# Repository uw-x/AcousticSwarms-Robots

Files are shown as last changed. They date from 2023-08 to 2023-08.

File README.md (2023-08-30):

## Hardware
The hardware design for the robots used in the acoustic swarms, including the circuits and PCB files.

## Firmware
This subfolder contains the source code for the firmware we upload on the robots. The firmware is compiled and uploaded using [Segger Embedded Studio v7.22](https://www.segger.com/downloads/embedded-studio/) and the [nRF5 SDK v17.0.1](https://www.nordicsemi.com/Products/Development-software/nRF5-SDK/Download#infotabs). 

## Receiver
This subfolder contains the source code and firmware for the receiver used to transmit data to and from the robot swarm. It also contains the 2D robot localization algorithm.

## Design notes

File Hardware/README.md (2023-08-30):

# Robot Hardware
This subfolder contains information pertaining to the robot design files.

## What's included
This folder contains the following directories:

**CAD**: STL files for the 3D models used. The base station is printed using an Ultimaker 3 with white PLA. The rest of the design files use a Formlabs Form 3 printer with black resin. The robot body takes inspiration from [Zooids](https://github.com/ShapeLab/SwarmUI), with various modifications. However, we use the 3D printed wheels are the same.

**Robot**: BoM & PCB design files for the robot main circuit.

**GyroHat**: BoM & PCB design files for the gyroscope hat on the top of the robot.

**SensorBars**: BoM & PCB design files for the sensor bar used to detect edges.

## How to use
To use these circuit design files, you will need the circuit design software KiCad. Simply import the schematics and PCB layouts into your preferred software and you can begin customizing and optimizing the design to fit your specific needs.

<p align="center">
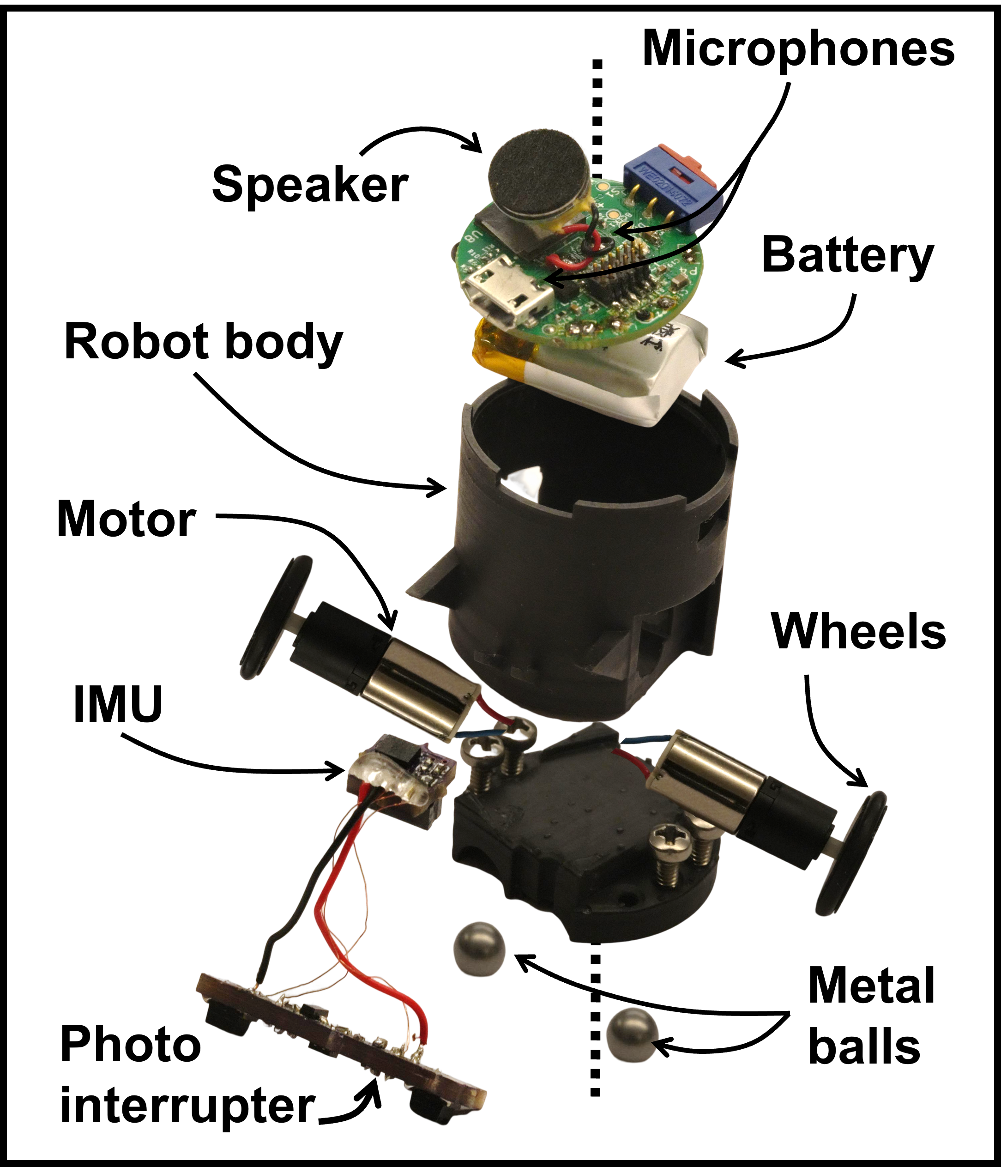
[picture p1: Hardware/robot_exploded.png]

</p>

During assembly, we place two wire connecting the metallic balls at the bottom of the robot to the PCB at the top. One ball is connected to the circuit ground while the other is connected through the +5V battery input (the Vin TestPoint in the PCB). For protection, this ball is connected through a [diode](https://www.digikey.com/ordering/shoppingcart?display=yes&itemSeqs=398627123,398628073,398633233&reprice=2).
We use [micro DC motors](https://www.firgelliauto.com/products/mini-motor-micro-motor) from Firgelli Auto.
We use [M2x0.4mm Thread, 6m Long screws](https://www.mcmaster.com/catalog/129/3394/90116A010) and [1/8 inch diameter aluminium balls](https://www.mcmaster.com/catalog/129/4186/34665K29) from McMaster-Carr.
We use [M1.5x8 Buna-N O-Ring](https://www.amazon.com/gp/product/B00595LLJK/ref=ppx_yo_dt_b_asin_title_o05_s00?ie=UTF8&th=1) from Amazon.

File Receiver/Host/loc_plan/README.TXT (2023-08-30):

1. initialization:
(1) Local_Node:
localization_node = Local_Node(initial_mean, initial_cov, alphas, beta, landmarks, init_angle_available, 'PF')

initial_mean - shape (3, 1), init pos of robot (x, y, theta) - (cm, cm, rad)
initial_cov - shape (3, 3) convariance matrix of init position, can use the example np.diag([0.2**2, 0.2**2, 0.1*2])
alphas - motion noise parameters need to be fine tune in experiment. Initailly use:  alphas = np.array([0.05**2, 0.005**2, 0.3**2, 0.005**2])
beta - chirp ranging noise, Initailly use: beta = np.diag([range_err**2, range_err**2, range_err**2]), where range_err = 0.7 cm
landmarks - shape (3, 2) position of three achors
init_angle_available - True - init angle is known; False - init angle is not known

(2) Planner node:
plan_node = Back_Planner(platform_W, platform_H, init_pos)

platform_W - the width of platform
platform_H - the height of platform
init_pos - the start point of robot, (x, y, theta) 
(destination is defalted by (0, 0))

2. Update 
(1) when the chirp data come, Call:
mean, velocity, particles = localization_node.update_offset(self, sample_offsets, self_offfset, old_pos = None, new_pos = None):

Input:
    sample_offsets - the sample offset from three achors - shape (3, 1)
    self_offfset - the samples offsets from self chirp - single number
    old_pos - the previous est position of robot - shape (3, ) (x, y, theta)
    new_pos - the current est potition of robot - shape (3, ) (x, y, theta)
Output:
    mean - the corretced potition of robot - shape (3, ) - (x, y, theta)
    velocity -  shape (2, 1) est velocity (vx, vy)
    particles - for debugging just ignore

(2) when the correction actions come, Call:
    localization_node.update_milestone(pos)

Input:
    pos - shape (3, ) the est position of the robot before rotating

(3) when the landmarks arrived, Call:

next_milestone, next_next_milestone = plan_node.update_milestone()

Output:
    next_milestone - next milestone, (x,y)
    next_next_milestone - the mile stone after the next milestone. 
The destination is [0, 0], when you is arriving or have arrived at [0, 0], 
the next_milestone returns (0, 0) and next_next_milestone returns (0, 1) for robot go further into the platform

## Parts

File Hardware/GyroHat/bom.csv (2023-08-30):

Component | Description | References | Value | Footprint | Quantity Per PCB | Datasheet | MANUFACTURER
1 | CAP CER 0.1UF 25V X5R 0402 | C2 | 100nF | C_0402_1005Metric | 1 | https://media.digikey.com/pdf/Data%20Sheets/Samsung%20PDFs/CL05A104KA5NNNC.pdf | Samsung Electro-Mechanics
2 | CONN HEADER SMD 12POS 1MM | J1 | FTMH-106-03-L-DV | SAMTEC_FTMH-106-03-L-DV | 1 | https://www.digikey.com/en/products/detail/samtec-inc/FTMH-106-03-L-DV/1104447 | SAMTEC
3 | RES SMD 10K OHM 5% 1/5W 0402 | R1 R2 R3 R4 | 10k | R_0402_1005Metric | 4 | https://fscdn.rohm.com/en/products/databook/datasheet/passive/resistor/chip_resistor/esr-e.pdf | Rohm Semiconductor
4 | INEMO INERTIAL MODULE | U2 | ISM330DLCTR | LGA-14_3x2.5mm_P0.5mm_LayoutBorder3x4y | 1 | https://www.digikey.com/en/products/detail/stmicroelectronics/ISM330DLCTR/7565501 | STMicroelectronics
Component Groups: | 4
Component Count: | 7
Fitted Components: | 7
Number of PCBs: | 1
Total components: | 7
Schematic Version:
Schematic Date:
PCB Variant: | default
BoM Date: | Fri 04 Aug 2023 09:19:59 AM
Schematic Source: | GyroHat.kicad_sch
KiCad Version: | Eeschema 6.0.2+dfsg-1

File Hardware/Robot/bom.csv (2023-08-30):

# | References | Value | Datasheet | Description | Manufacturer | Manufacturer P/N | Vendor | Vendor P/N | Quantity | Notes
1 | > C3, C8 | dnp |  | Do Not Place |  |  |  |  | 2
2 | > C4, C5 | 4.7uF | https://media.digikey.com/pdf/Data%20Sheets/Samsung%20PDFs/CL10A475KQ8NNNC_Spec.pdf | CAP CER 4.7UF 10V X5R 0603 | Samsung Electro-Mechanics | CL10A475KQ8NNNC | Digi-key | 1276-1045-2-ND | 2
3 | C7 | 10uF | https://datasheets.kyocera-avx.com/x6s-dielectric.pdf | CAP CER 10UF 16V X6S 0603 | KYOCERA AVX | 0603YW106MAT2A | Digi-key | 478-0603YW106MAT2ATR-ND | 1
4 | > C1, C2, C6, C10-C12, C14 | 100nF | https://media.digikey.com/pdf/Data%20Sheets/Samsung%20PDFs/CL05A104KA5NNNC.pdf | CAP CER 0.1UF 25V X5R 0402 | Samsung Electro-Mechanics | CL05A104KA5NNNC | Digi-key | 1276-1043-2-ND | 7
5 | J1 | 10118194-0001LF | https://cdn.amphenol-icc.com/media/wysiwyg/files/documentation/datasheet/inputoutput/io_usb_micro.pdf | USB - micro B USB 2.0 Receptacle Connector 5 Position Surface Mount, Right Angle; Through Hole | Amphenol ICC (FCI) | 10118194-0001LF | Digi-key | 609-4618-2-ND | 1
6 | J2 | FTMH-106-03-L-DV | https://www.mouser.com/datasheet/2/527/ftmh_sm-2854321.pdf | Board to Board & Mezzanine Connectors 1.00 mm Surface Mount Micro Terminal Strip | Samtec | FTMH-106-03-L-DV | Mouser | 200-FTMH10603LDV | 1
7 | L1 | 2.2u | https://search.murata.co.jp/Ceramy/image/img/P02/J(E)TE243A-0029_DFE201210U_reference.pdf | 2.2 µH Shielded Wirewound Inductor 1.2 A 228mOhm Max 0805 (2012 Metric) - | Murata Electronics | DFE201210U-2R2M=P2 | Digi-key | 490-16592-2-ND | 1
8 | > MK1, MK2 | ICS-41352 | https://invensense.tdk.com/wp-content/uploads/2016/10/DS-000048-ICS-41352-data-sheet-v1.0.pdf | Bottom Port PDM Low Power muti-Mode Microphone with high AOP Mode | TDK-InvenSense | ICS-41352 | Digi-key | 1428-ICS-41352TR-ND | 2
9 | P1 | BATT_TERM | https://www.jst-mfg.com/product/pdf/eng/eACH.pdf | Connector Header Surface Mount, Right Angle 2 position 0.047" (1.20mm) | JST Sales America Inc. | BM02B-ACHSS-GAN-ETF(LF)(SN | Digi-key | 455-3277-2-ND | 1
10 | P3 | M2_TERM |  | Do Not Place |  |  |  |  | 1 | Solder motor leads here
11 | P4 | M1_TERM |  | Do Not Place |  |  |  |  | 1 | Solder motor leads here
12 | > R1, R3 | 50R | https://www.yageo.com/upload/media/product/productsearch/datasheet/rchip/PYu-AC_51_RoHS_L_10.pdf | RES SMD 50 OHM 5% 1/16W 0402 | YAGEO | AC0402JR-0750RL | Digi-key | 13-AC0402JR-0750RLTR-ND | 2
13 | R2 | 180R | https://www.te.com/usa-en/product-5-2176337-2.datasheet.pdf | RES 180 OHM 1% 1/16W 0402 | TE Connectivity Passive Product | CRGCQ0402F180K | Digi-key | A129654TR-ND | 1
14 | > R4, R5, R7 | 10K | https://fscdn.rohm.com/en/products/databook/datasheet/passive/resistor/chip_resistor/esr-e.pdf | RES SMD 10K OHM 5% 1/5W 0402 | Rohm Semiconductor | ESR01MZPJ103 | Digi-key | RHM1003TR-ND | 3
15 | > R6, R11, R12 | dnp |  | Do Not Place |  |  |  |  | 3
16 | R8 | 100K | https://www.yageo.com/upload/media/product/productsearch/datasheet/rchip/PYu-RT_1-to-0.01_RoHS_L_15.pdf | RES SMD 100K OHM 0.1% 1/16W 0402 | YAGEO | RT0402BRE07100KL | Digi-key | YAG2304TR-ND | 1
17 | > R9, R10, R13 | 0R | https://www.seielect.com/Catalog/SEI-RMCF_RMCP.pdf | RES 0 OHM JUMPER 1/16W 0402 | Stackpole Electronics Inc | RMCF0402ZT0R00 | Digi-key | RMCF0402ZT0R00TR-ND | 3
18 | S1 | 450302014072 | http://www.farnell.com/datasheets/1913864.pdf | Through Hole Slide Switch SPDT On-On 100 mA@ 42 V dc Slide | Wurth Elektronik | 450302014072 | Mouser | 710-450302014072 | 1
19 | SP1 | SPEAKER | http://puiaudio.com/pdf/AS01008MR-3-LW100-R.pdf | 8 Ohms General Purpose Speaker 500 mW 800 Hz ~ 20 kHz Top Round | PUI Audio, Inc. | AS01008MR-3-LW100-R | Digi-key | 668-AS01008MR-3-LW100-R-ND | 1 | Footprint should not match speaker. During fabrication, DO NOT PLACE ANY COMPONENT HERE. Manually solder speaker leads after receiving boards instead.
20 | U1 | B38G3RGB | https://media.digikey.com/pdf/Data%20Sheets/Harvatek%20PDFs/B38G3RGB-10D0003H2U1930%20%20V1.9.pdf | Red, Green, Blue (RGB) - LED Indication - Discrete 2V Red, 3V Green, 3V Blue 0606 (1616 Metric) | Harvatek Corporation | B38G3RGB-10D0003H2U1930 | Digi-key | 3147-B38G3RGB-10D0003H2U1930TR-ND | 1
21 | U2 | LM3671TLX-3.3_NOPB | https://www.ti.com/general/docs/suppproductinfo.tsp?distId=10 | Buck Switching Regulator IC Positive Fixed 3.3V 1 Output 600mA 5-WFBGA, DSBGA | Texas Instruments | LM3671TLX-3.3/NOPB | Digi-key | LM3671TLX-3.3/NOPBTR-ND | 1
22 | U3 | LTC4124 | https://www.analog.com/media/en/technical-documentation/data-sheets/ltc4124.pdf | Wireless Charging ICs 100mA Wireless Li-Ion Charger | Analog Devices | LTC4124EV#TRMPBF | Mouser | 584-LTC4124EV#TRMPBF | 1
23 | U4 | MAX17048G+T10 | https://datasheets.maximintegrated.com/en/ds/MAX17048-MAX17049.pdf | IC BATT MON LI-ION 1CELL 8TDFN | Analog Devices Inc./Maxim Integrated | MAX17048G+T10 | Digi-key | MAX17048G+T10TR-ND | 1
24 | > U5, U6 | DRV8837CDSGR | https://www.ti.com/general/docs/suppproductinfo.tsp?distId=10 | IC HALF-BRIDGE DRVR PWM 8WSON | Texas Instruments | DRV8837CDSGR | Digi-key | 296-47205-2-ND | 2
25 | U7 | MC3419 | https://www.mouser.com/datasheet/2/821/MEMSIC_MC3419_Datasheet-1889799.pdf | Accelerometers Small Digital 3-axis Accelerometer Sensor | MEMSIC | MC3419 | Mouser | 498-MC3419 | 1
26 | U8 | ISP1807-LR-RS | https://www.insightsip.com/fichiers_insightsip/pdf/ble/ISP1807/isp_ble_DS1807.pdf | Bluetooth Bluetooth v5.0, Thread, Zigbee® Transceiver Module 2.402GHz ~ 2.48GHz Integrated, Trace Surface Mount | Insight SIP | ISP1807-LR-RS | Digi-key | 1786-1019-2-ND | 1
27 | U9 | MAX98357A | https://datasheets.maximintegrated.com/en/ds/MAX98357A-MAX98357B.pdf | IC AMP CLASS D MONO 3.2W 9WLP | Analog Devices Inc./Maxim Integrated | MAX98357AEWL+T | Digi-key | MAX98357AEWL+TTR-ND | 1

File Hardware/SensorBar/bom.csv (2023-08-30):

Component | Description | References | Value | Footprint | Quantity Per PCB | Datasheet
1 | CAP CER 0.1UF 25V X5R 0402 | C1 C2 C3 | 100nF | C_0402_1005Metric | 3 | https://media.digikey.com/pdf/Data%20Sheets/Samsung%20PDFs/CL05A104KA5NNNC.pdf
2 | CAP CER 10UF 16V X6S 0603 | C4 | 10uF | C_0402_1005Metric | 1 | https://datasheets.kyocera-avx.com/x6s-dielectric.pdf
3 | TRANS NPN 45V 0.5A TO236AB | Q1 | Q_NPN_BEC | SOT-23 | 1 | https://www.digikey.com/en/products/detail/nexperia-usa-inc/BC817-40-215/763235
4 | RES 100 OHM 1% 1/16W 0402 | R2 R4 | 100 | R_0402_1005Metric | 2 | https://www.vishay.com/docs/28705/mcx0x0xpro.pdf
5 | RES 1K OHM 1% 1/16W 0402 | R1 | 1k | R_0402_1005Metric | 1 | https://www.yageo.com/upload/media/product/productsearch/datasheet/rchip/PYu-AC_51_RoHS_L_10.pdf
6 | RES SMD 10K OHM 5% 1/5W 0402 | R6 R7 R8 | 10k | R_0402_1005Metric | 3 | https://fscdn.rohm.com/en/products/databook/datasheet/passive/resistor/chip_resistor/esr-e.pdf
7 | RES 30K OHM 1% 1/16W 0402 | R3 R5 | 30k | R_0402_1005Metric | 2 | https://www.digikey.com/en/products/detail/yageo/RC0402FR-0730KL/726586
8 | PHOTOINTERRUPTER REFLEC 3MM SMD | U1 U2 | GP2S700HCP | GP2S700HCP | 2 | https://global.sharp/products/device/lineup/data/pdf/datasheet/gp2s700hcp_e.pdf
9 | IC COMPARATOR 2 GEN PUR 8UFSON | U3 | LM293QT | DFN-8-1EP_2x2mm_P0.5mm_EP0.6x1.2mm | 1 | https://www.st.com/content/ccc/resource/technical/document/datasheet/group1/b4/cc/cf/13/18/28/44/f5/CD00000465/files/CD00000465.pdf/jcr:content/translations/e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
Component Groups: | 10
Component Count: | 17
Fitted Components: | 16
Number of PCBs: | 1
Total components: | 16
Schematic Version:
Schematic Date:
PCB Variant: | default
BoM Date: | Fri 04 Aug 2023 09:10:59 AM
Schematic Source: | SensorBar.kicad_sch
KiCad Version: | Eeschema 6.0.2+dfsg-1

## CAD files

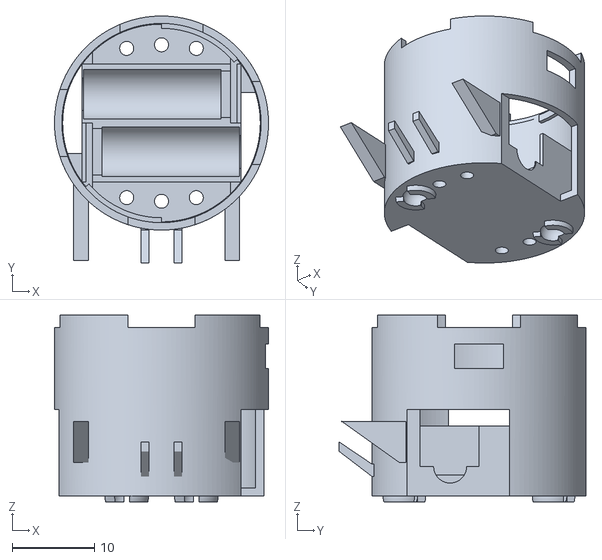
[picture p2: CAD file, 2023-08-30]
Hardware/CAD/BaseDC-Base.stl
26.0 x 30.0 x 22.7

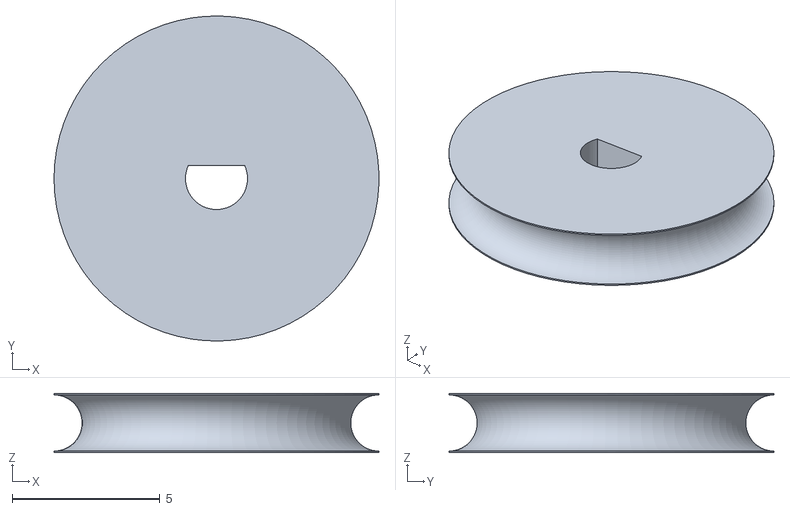
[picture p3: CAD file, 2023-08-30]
Hardware/CAD/WheelWithSlot.STL
11.0 x 11.0 x 2.00

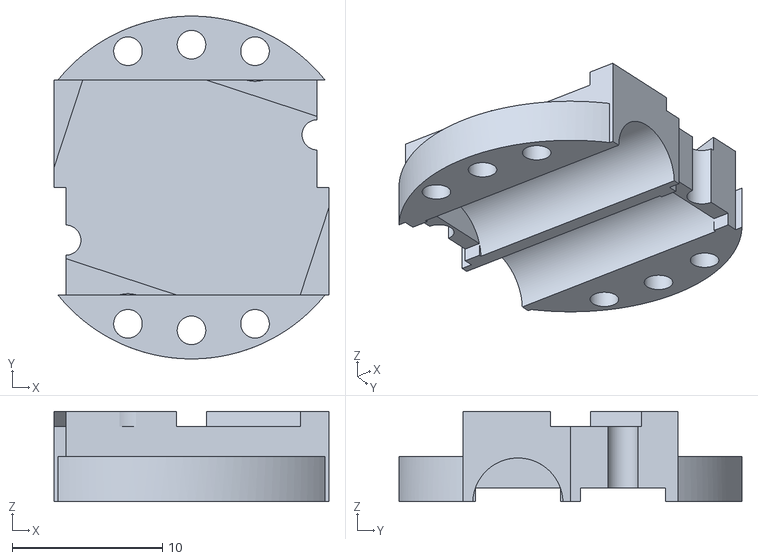
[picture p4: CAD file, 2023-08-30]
Hardware/CAD/RobotMotorTop.stl
18.3 x 22.8 x 6.00

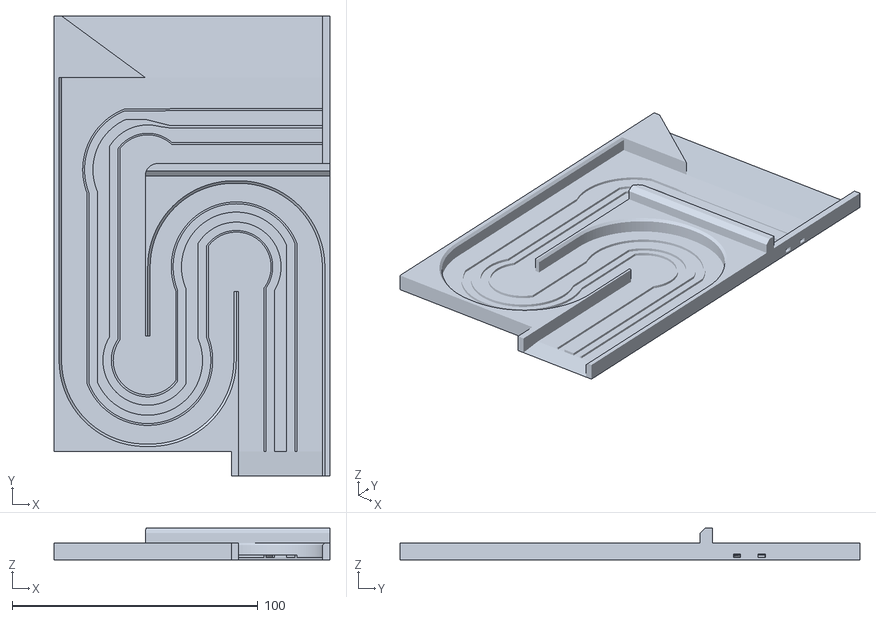
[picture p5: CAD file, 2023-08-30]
Hardware/CAD/Stationv5.3_1.1mm.stl
112.0 x 187.0 x 13.0

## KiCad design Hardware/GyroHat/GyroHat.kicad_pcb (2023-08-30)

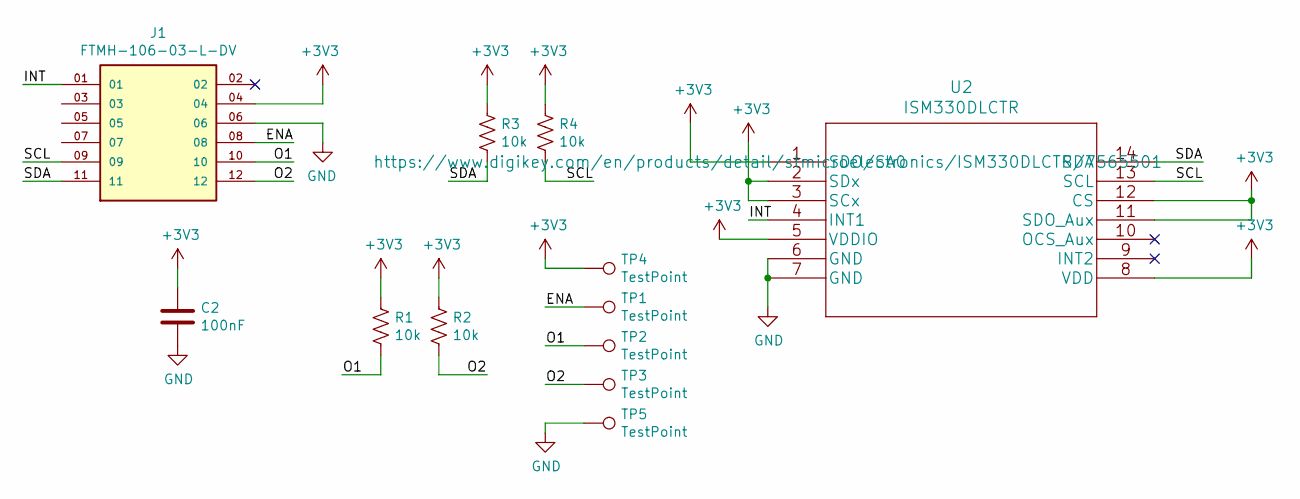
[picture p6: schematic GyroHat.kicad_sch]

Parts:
C2: 100nF; C_0402_1005Metric
J1: FTMH-106-03-L-DV; SAMTEC_FTMH-106-03-L-DV
R1, R2, R3, R4: 10k; R_0402_1005Metric
TP1, TP2, TP3, TP4, TP5: TestPoint; Wire Pad
U2: ISM330DLCTR; LGA-14_3x2.5mm_P0.5mm_LayoutBorder3x4y

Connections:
+3V3: C2.1, J1.04, R1.1, R2.1, R3.1, R4.1, TP4.1, U2.1 (SDO/SA0), U2.2 (SDx), U2.3 (SCx), U2.5 (VDDIO), U2.8 (VDD), U2.11 (SDO_Aux), U2.12 (CS)
/ENA: J1.08, TP1.1
/INT: J1.01, U2.4 (INT1)
/O1: J1.10, R1.2, TP2.1
/O2: J1.12, R2.2, TP3.1
/SCL: J1.09, R4.2, U2.13 (SCL)
/SDA: J1.11, R3.2, U2.14 (SDA)
GND: C2.2, J1.06, TP5.1, U2.6 (GND), U2.7 (GND)

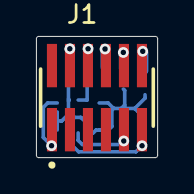
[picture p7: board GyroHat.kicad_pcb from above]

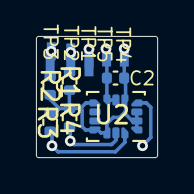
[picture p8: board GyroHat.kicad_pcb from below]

Board: 2 copper layers, 6.7 x 6.7 mm, 12 parts (11 on the bottom side), 8 nets.

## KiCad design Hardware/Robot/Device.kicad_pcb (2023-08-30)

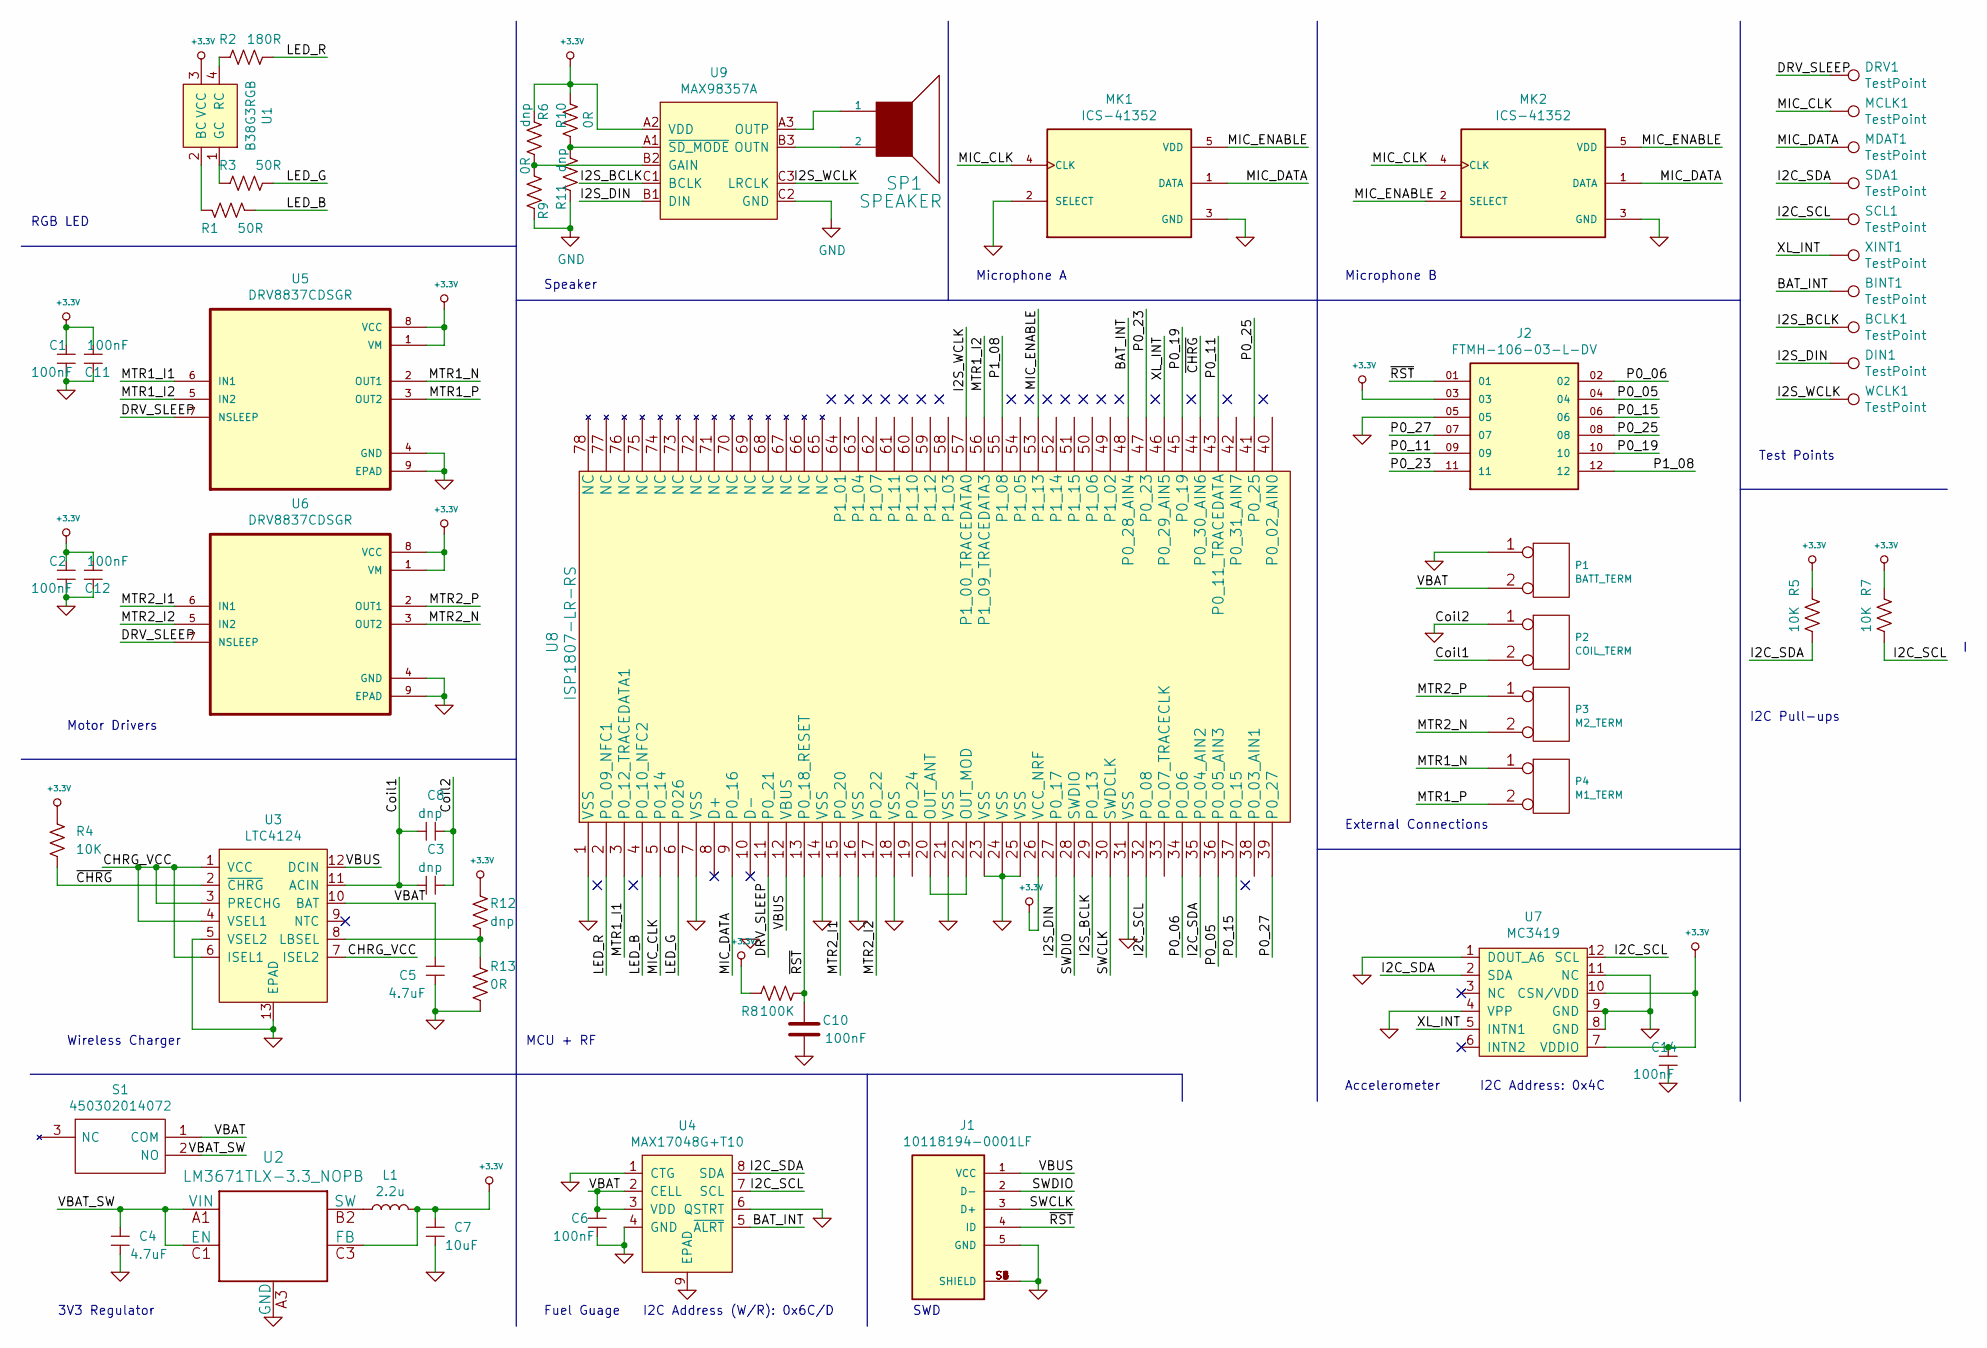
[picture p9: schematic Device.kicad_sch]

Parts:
BCLK1: TestPoint; TestPoint_Pad_D1.0mm
BINT1: TestPoint; TestPoint_Pad_D1.0mm
C1, C2, C6, C10, C11, C12, C14: 100nF; C_0402_1005Metric; Manufacturer P/N CL05A104KA5NNNC
C3, C8: dnp; C_0402_1005Metric
C4, C5: 4.7uF; C_0603_1608Metric; Manufacturer P/N CL10A475KQ8NNNC
C7: 10uF; C_0603_1608Metric; Manufacturer P/N 0603YW106MAT2A
DIN1: TestPoint; TestPoint_Pad_D1.0mm
DRV1: TestPoint; TestPoint_Pad_D1.0mm
J1: 10118194-0001LF; AMPHENOL_10118194-0001LF; PARTREV B
J2: FTMH-106-03-L-DV; SAMTEC_FTMH-106-03-L-DV; Manufacturer P/N FTMH-106-03-L-DV
L1: 2.2u; L_0805_2012Metric; Manufacturer P/N DFE201210U-2R2M=P2
MCLK1: TestPoint; TestPoint_Pad_D1.0mm
MDAT1: TestPoint; TestPoint_Pad_D1.0mm
MK1, MK2: ICS-41352; MIC_ICS-41350; Manufacturer P/N ICS-41352
P1: BATT_TERM; JST_ACH_BM02B-ACHSS-GAN-ETF_1x02-1MP_P1.20mm_Vertical; Manufacturer P/N BM02B-ACHSS-GAN-ETF(LF)(SN
P2: COIL_TERM; TestPoint_2Pads_Pitch2.54mm_Drill0.8mm
P3: M2_TERM; PinHeader_1x02_P1.27mm_Vertical
P4: M1_TERM; PinHeader_1x02_P1.27mm_Vertical
R1, R3: 50R; R_0402_1005Metric; Manufacturer P/N AC0402JR-0750RL
R2: 180R; R_0402_1005Metric; Manufacturer P/N CRGCQ0402F180K
R4, R5, R7: 10K; R_0402_1005Metric; Manufacturer P/N ESR01MZPJ103
R6, R11, R12: dnp; R_0402_1005Metric
R8: 100K; R_0402_1005Metric; Manufacturer P/N RT0402BRE07100KL
R9, R10, R13: 0R; R_0402_1005Metric; Manufacturer P/N RMCF0402ZT0R00
S1: 450302014072; Manufacturer P/N 450302014072
SCL1: TestPoint; TestPoint_Pad_D1.0mm
SDA1: TestPoint; TestPoint_Pad_D1.0mm
SP1: SPEAKER; CUI_CMT-4023S-SMT-TR; Manufacturer P/N SMT-0440-T-HT-R
U1: B38G3RGB; B38G3RGB10D0003H2U1930; Manufacturer P/N B38G3RGB-10D0003H2U1930
U2: LM3671TLX-3.3_NOPB; LM3671TLX-3.3&slash_NOPB; Manufacturer P/N LM3671TLX-3.3/NOPB
U3: LTC4124; LTC4124EV-TRMPBF; Manufacturer P/N LTC4124EV#TRMPBF
U4: MAX17048G+T10; SON50P200X200X80-9N; Manufacturer P/N MAX17048G+T10
U5, U6: DRV8837CDSGR; SON50P200X200X80-9N; Manufacturer P/N DRV8837CDSGR
U7: MC3419; LGA-12_2x2mm_P0.5mm; Manufacturer P/N MC3419
U8: ISP1807-LR-RS; Manufacturer P/N ISP1807-LR-RS
U9: MAX98357A; Maxim_WLP-9_1.595x1.415_Layout3x3_P0.4mm_Ball0.27mm_Pad0.25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; Manufacturer P/N MAX98357AEWL+T
WCLK1: TestPoint; TestPoint_Pad_D1.0mm
XINT1: TestPoint; TestPoint_Pad_D1.0mm

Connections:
+3.3V: C1.1, C2.1, C7.2, C11.2, C12.2, C14.1, J2.03, L1.2, R4.1, R5.1, R6.2, R7.1, R8.1, R10.1, R12.1, U1.3 (VCC), U2.C3 (FB), U5.1 (VM), U5.8 (VCC), U6.1 (VM), U6.8 (VCC), U7.7 (VDDIO), U7.10 (CSN/VDD), U8.26 (VCC_NRF), U9.A2 (VDD)
/BAT_INT: BINT1.1, U4.5 (~ALRT), U8.48 (P0_28_AIN4)
/CHRG_VCC: U3.1 (VCC), U3.3 (PRECHG), U3.4 (VSEL1), U3.6 (ISEL1), U3.7 (ISEL2)
/Coil1: C3.2, C8.2, P2.2 (PM), U3.11 (ACIN)
/DRV_SLEEP: DRV1.1, U5.7 (NSLEEP), U6.7 (NSLEEP), U8.11 (P0_21)
/I2C_SCL: R7.2, SCL1.1, U4.7 (SCL), U7.12 (SCL), U8.32 (P0_08)
/I2C_SDA: R5.2, SDA1.1, U4.8 (SDA), U7.2 (SDA), U8.35 (P0_04_AIN2)
/I2S_BCLK: BCLK1.1, U8.29 (P0_13), U9.C1 (BCLK)
/I2S_DIN: DIN1.1, U8.27 (P0_17), U9.B1 (DIN)
/I2S_WCLK: U8.57 (P1_00_TRACEDATA0), U9.C3 (LRCLK), WCLK1.1
/LED_B: R1.2, U8.4 (P0_10_NFC2)
/LED_G: R3.2, U8.6 (P026)
/LED_R: R2.2, U8.2 (P0_09_NFC1)
/MIC_CLK: MCLK1.1, MK1.4 (CLK), MK2.4 (CLK), U8.5 (P0_14)
/MIC_DATA: MDAT1.1, MK1.1 (DATA), MK2.1 (DATA), U8.9 (P0_16)
/MIC_ENABLE: MK1.5 (VDD), MK2.2 (SELECT), MK2.5 (VDD), U8.53 (P1_13)
/MTR1_I1: U5.6 (IN1), U8.3 (P0_12_TRACEDATA1)
/MTR1_I2: U5.5 (IN2), U8.56 (P1_09_TRACEDATA3)
/MTR1_N: P4.1, U5.2 (OUT1)
/MTR1_P: P4.2 (PM), U5.3 (OUT2)
/MTR2_I1: U6.6 (IN1), U8.15 (P0_20)
/MTR2_I2: U6.5 (IN2), U8.17 (P0_22)
/MTR2_N: P3.2 (PM), U6.3 (OUT2)
/MTR2_P: P3.1, U6.2 (OUT1)
/P0_05: J2.04, U8.36 (P0_05_AIN3)
/P0_06: J2.02, U8.34 (P0_06)
/P0_11: J2.09, U8.43 (P0_11_TRACEDATA)
/P0_15: J2.06, U8.37 (P0_15)
/P0_19: J2.10, U8.45 (P0_19)
/P0_23: J2.11, U8.47 (P0_23)
/P0_25: J2.08, U8.41 (P0_25)
/P0_27: J2.07, U8.39 (P0_27)
/P1_08: J2.12, U8.55 (P1_08)
/SWCLK: J1.3 (D+), U8.30 (SWDCLK)
/SWDIO: J1.2 (D-), U8.28 (SWDIO)
/VBAT: C5.1, C6.2, P1.2 (PM), S1.1 (COM), U3.10 (BAT), U4.2 (CELL), U4.3 (VDD)
/VBAT_SW: C4.2, S1.2 (NO), U2.A1 (VIN), U2.C1 (EN)
/VBUS: J1.1 (VCC), U3.12 (DCIN), U8.12 (VBUS)
/XL_INT: U7.5 (INTN1), U8.46 (P0_29_AIN5), XINT1.1
/~CHRG: R4.2, U3.2 (~CHRG), U8.44 (P0_30_AIN6)
/~RST: C10.1, J1.4 (ID), J2.01, R8.2, U8.13 (P0_18_RESET)
GND: C1.2, C2.2, C3.1, C4.1, C5.2, C6.1, C7.1, C8.1, C10.2, C11.1, C12.1, C14.2, J1.5 (GND), J1.S1 (SHIELD), J1.S2 (SHIELD), J1.S3 (SHIELD), J1.S4 (SHIELD), J1.S5 (SHIELD), J1.S6 (SHIELD), J2.05, MK1.2 (SELECT), MK1.3 (GND), MK2.3 (GND), P1.1, P2.1, R9.1, R11.1, R13.2, U2.A3 (GND), U3.5 (VSEL2), U3.13 (EPAD), U4.1 (CTG), U4.4 (GND), U4.6 (QSTRT), U4.9 (EPAD), U5.4 (GND), U5.9 (EPAD), U6.4 (GND), U6.9 (EPAD), U7.1 (DOUT_A6), U7.4 (VPP), U7.8 (GND), U7.9 (GND), U7.11 (NC), U8.1 (VSS), U8.7 (VSS), U8.14 (VSS), U8.16 (VSS), U8.18 (VSS), U8.21 (VSS), U8.23 (VSS), U8.24 (VSS), U8.25 (VSS), U8.31 (VSS), U9.C2 (GND)
unnamed: L1.1, U2.B2 (SW)
unnamed: R1.1, U1.2 (BC)
unnamed: R2.1, U1.4 (RC)
unnamed: R3.1, U1.1 (GC)
unnamed: R6.1, R9.2, U9.B2 (GAIN)
unnamed: R10.2, R11.2, U9.A1 (~SD_MODE)
unnamed: R12.2, R13.1, U3.8 (LBSEL)
unnamed: SP1.1, U9.A3 (OUTP)
unnamed: SP1.2, U9.B3 (OUTN)
unnamed: U8.20 (OUT_ANT), U8.22 (OUT_MOD)

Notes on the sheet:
3V3 Regulator
I2C Pull-ups
Test Points
Wireless Charger
SWD
MCU + RF
RGB LED
Motor Drivers
Speaker
Fuel Guage
Microphone B
External Connections
Accelerometer
Microphone A
I2C Address: 0x4C
I2C Address (W/R): 0x6C/D

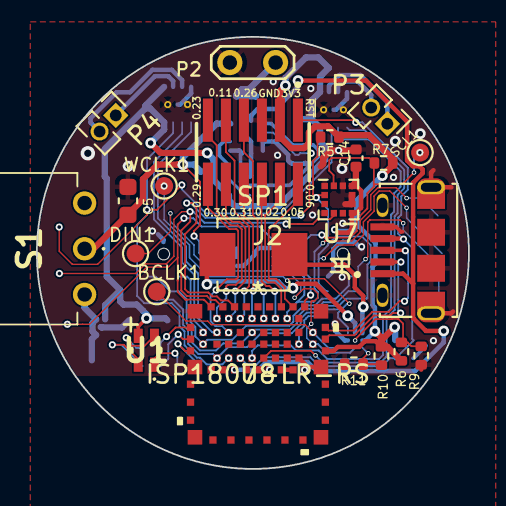
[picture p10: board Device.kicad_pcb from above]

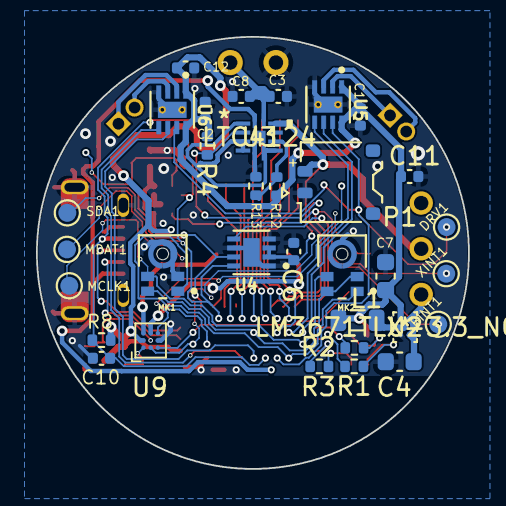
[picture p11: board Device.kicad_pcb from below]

Board: 2 copper layers, 24.0 x 24.0 mm, 55 parts (33 on the bottom side), 52 nets.

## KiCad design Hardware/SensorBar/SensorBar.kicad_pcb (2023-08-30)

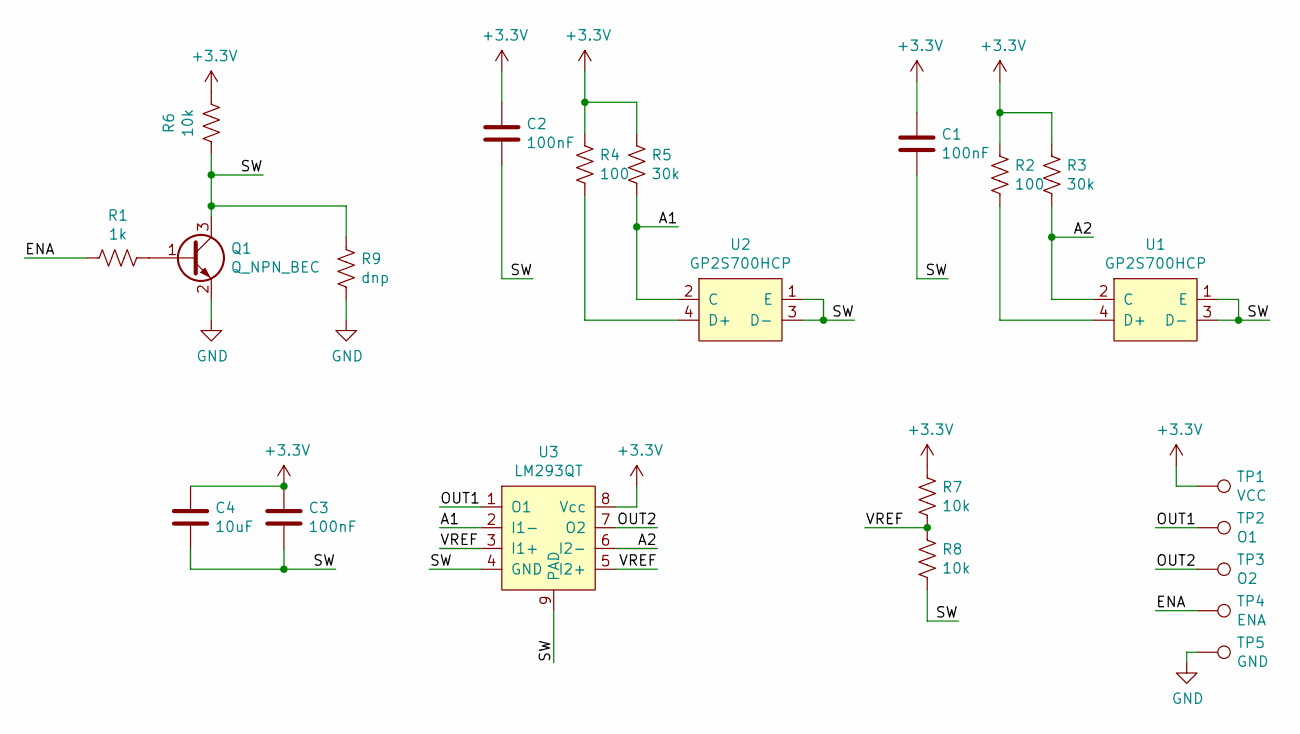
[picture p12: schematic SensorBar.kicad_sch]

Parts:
C1, C2, C3: 100nF; C_0402_1005Metric
C4: 10uF; C_0402_1005Metric
Q1: Q_NPN_BEC; SOT-23
R1: 1k; R_0402_1005Metric
R2, R4: 100; R_0402_1005Metric
R3, R5: 30k; R_0402_1005Metric
R6, R7, R8: 10k; R_0402_1005Metric
R9: dnp; R_0402_1005Metric
TP1: VCC; TestPoint_Pad_D1.0mm
TP2: O1; TestPoint_Pad_D1.0mm
TP3: O2; TestPoint_Pad_D1.0mm
TP4: ENA; TestPoint_Pad_D1.0mm
TP5: GND; TestPoint_Pad_D1.0mm
U1, U2: GP2S700HCP
U3: LM293QT; DFN-8-1EP_2x2mm_P0.5mm_EP0.6x1.2mm

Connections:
+3V3: C1.1, C2.1, C3.1, C4.1, R2.2, R3.2, R4.2, R5.2, R6.1, R7.2, TP1.1, U3.8 (Vcc)
/A1: R5.1, U2.2 (C), U3.2 (I1-)
/A2: R3.1, U1.2 (C), U3.6 (I2-)
/ENA: R1.2, TP4.1
/OUT1: TP2.1, U3.1 (O1)
/OUT2: TP3.1, U3.7 (O2)
/SW: C1.2, C2.2, C3.2, C4.2, Q1.3 (C), R6.2, R8.1, R9.2, U1.1 (E), U1.3 (D-), U2.1 (E), U2.3 (D-), U3.4 (GND), U3.9 (PAD)
/VREF: R7.1, R8.2, U3.3 (I1+), U3.5 (I2+)
GND: Q1.2 (E), R9.1, TP5.1
unnamed: Q1.1 (B), R1.1
unnamed: R2.1, U1.4 (D+)
unnamed: R4.1, U2.4 (D+)

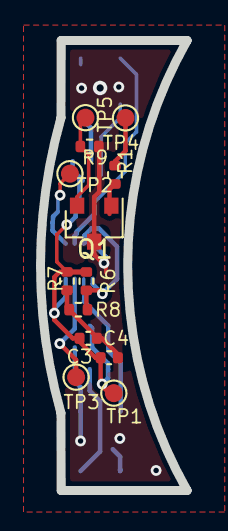
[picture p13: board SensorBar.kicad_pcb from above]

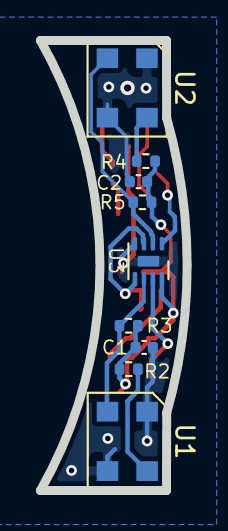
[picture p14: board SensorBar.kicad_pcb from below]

Board: 2 copper layers, 8.1 x 25.0 mm, 22 parts (9 on the bottom side), 12 nets.

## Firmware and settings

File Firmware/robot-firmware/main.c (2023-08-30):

// MAKE SURE ROBOT NAME IS SHIO NOT SHIOG

/**
 * Copyright (c) 2014 - 2021, Nordic Semiconductor ASA
 *
 * All rights reserved.
 *
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
 * 3. Neither the name of Nordic Semiconductor ASA nor the names of its
 *    contributors may be used to endorse or promote products derived from this
 *    software without specific prior written permission.
 *
 * 4. This software, with or without modification, must only be used with a
 *    Nordic Semiconductor ASA integrated circuit.
 *
 * 5. Any software provided in binary form under this license must not be reverse
 *    engineered, decompiled, modified and/or disassembled.
 *
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
 */
/** @file
 *
 * @defgroup ble_sdk_app_template_main main.c
 * @{
 * @ingroup ble_sdk_app_template
 * @brief Template project main file.
 *
 * This file contains a template for creating a new application. It has the code necessary to wakeup
 * from button, advertise, get a connection restart advertising on disconnect and if no new
 * connection created go back to system-off mode.
 * It can easily be used as a starting point for creating a new application, the comments identified
 * with 'YOUR_JOB' indicates where and how you can customize.
 */

 
#include <assert.h>

#include <stdbool.h>
#include <stdint.h>
#include <string.h>

#include "nordic_common.h"
#include "nrf.h"

#include "app_error.h"
#include "nrf_sdh.h"
#include "nrf_sdh_soc.h"
#include "app_timer.h"
#include "app_util_platform.h"

#include "peer_manager.h"
#include "peer_manager_handler.h"
#include "nrf_pwr_mgmt.h"

#include "nrf_log.h"
#include "nrf_log_ctrl.h"
#include "nrf_log_default_backends.h"

#include "nrf_ppi.h"
#include "nrf_timer.h"
#include "nrf_egu.h"

#include "gpio.h"
#include "ble_manager.h"
#include "event.h"
#include "timers.h"
#include "ble_config.h"
#include "time_sync.h"
#include "audio.h"

#include "led.h"
#include "bsp_btn_ble.h"
#include "i2c.h"
#include "i2s.h"
#include "buzzer.h"
#include "fuel_gauge.h"
#include "accel.h"
#include "motors.h"
#include "recorder.h"
#include "ts_tasks.h"
#include "charger.h"
#include "nav.h"
#include "point.h"
#include "gyro.h"
#include "channel_utils.h"
#include "ir.h"
#include "ble_dcs.h"
#include "profile.h"


// In case something is going wrong, check on both receiver & robots:
// Always use stack allocation for ringbuffers!!
// Always compile as release!!

APP_TIMER_DEF(resetTimer);

static uint8_t micData[PACKET_LENGTH];
static bool bleRetry = false;

static bool m_pdm_started = false;
static bool m_stream_started = false;
static uint32_t m_interval = 0;

static bool m_audio_data_requested = false;

// Enough for 250 ms @ 50kHz (as int16)
//#define RECORDING_BUFFER_SIZE 35000

// Enough for 50 ms @ 62.5kHz (as int16)
#define RECORDING_BUFFER_SIZE (6500 * 2)
//#define RECORDING_BUFFER_SIZE 8
static int16_t rec_single_channel_buffer[3126];

#define SHIELD_ENABLED 1

static uint8_t m_record_buffer[RECORDING_BUFFER_SIZE] = {0};
static recording_t s_recording;

static uint64_t expectedBufferCount = 0;

static int64_t m_audio_buffer_samples = 0;

static bool m_sensor_notifications_enabled = false;

/**@brief Callback function for asserts in the SoftDevice.
 *
 * @details This function will be called in case of an assert in the SoftDevice.
 *
 * @warning This handler is an example only and does not fit a final product. You need to analyze
 *          how your product is supposed to react in case of Assert.
 * @warning On assert from the SoftDevice, the system can only recover on reset.
 *
 * @param[in] line_num   Line number of the failing ASSERT call.
 * @param[in] file_name  File name of the failing ASSERT call.
 */
void assert_nrf_callback(uint16_t line_num, const uint8_t * p_file_name)
{
    NRF_LOG_RAW_INFO("DEADBEEF: SOFTDEVICE INTERNAL ERRROR IN %s AT LINE %d\n", p_file_name, line_num);
    app_error_handler(DEAD_BEEF, line_num, p_file_name);
}


/**@brief Function for putting the chip into sleep mode.
 *
 * @note This function will not return.
 */
static void sleep_mode_enter(void)
{
    ret_code_t err_code;

    err_code = led_indicate(LED_OFF);

    // Prepare wakeup buttons.
    //err_code = bsp_btn_ble_sleep_mode_prepare();
    //APP_ERROR_CHECK(err_code);

    // Go to system-off mode (this function will not return; wakeup will cause a reset).
    err_code = sd_power_system_off();
    APP_ERROR_CHECK(err_code);
}


/**@brief Function for initializing the nrf log module.
 */
static void log_init(void)
{
    ret_code_t err_code = NRF_LOG_INIT(NULL);
    APP_ERROR_CHECK(err_code);

    NRF_LOG_DEFAULT_BACKENDS_INIT();
}


/**@brief Function for initializing power management.
 */
static void power_management_init(void)
{
    ret_code_t err_code;
    err_code = nrf_pwr_mgmt_init();
    APP_ERROR_CHECK(err_code);
}

void powerEnterSleepMode(void)
{
  ret_code_t err_code;

  NRF_LOG_RAW_INFO("%08d [power] powering off...\n", systemTimeGetMs());

  err_code = led_indicate(LED_OFF);
  APP_ERROR_CHECK(err_code);
  
  motors_deinit();
  accel_deinit();
  
#if SHIELD_ENABLED
  gyro_deinit();
#endif
  
  // Don't ?
  //fg_deinit();
  
  i2c_deinit();
  i2s_deinit();
  audioDeInit();

  led_deinit();
  ir_disable();

  ////spiDeInit();
  //delayMs(1);

  NRF_LOG_RAW_INFO("%08d [power] Shut down.\n", systemTimeGetMs());
  // Go to system-off mode (this function will not return; wakeup will cause a reset).
  err_code = sd_power_system_off();
  APP_ERROR_CHECK(err_code);
}

/**@brief Function for handling the idle state (main loop).
 *
 * @details If there is no pending log operation, then sleep until next the next event occurs.
 */
static void idle_state_handle(void){
    if (NRF_LOG_PROCESS() == false){
        nrf_pwr_mgmt_run();
    }
}

static void resetTimerCallback(void * p_context){
  NVIC_SystemReset();
}

void TIMER3_IRQHandler(){
  if(NRF_TIMER3->EVENTS_COMPARE[4]){
    if(!ts_sync_tasks_started()){
      ts_sync_tasks_start(true);
      NRF_LOG_RAW_INFO("%08d [main] TIME SYNC MASTER\n", systemTimeGetMs());
    }else{
      NRF_LOG_INFO("Disabling PPIs");
      ts_sync_tasks_disable_pending_ppis();
    }
    NRF_TIMER3->EVENTS_COMPARE[4] = 0;
    // Disable interrupt (this is supposed to be a one time thing)
    NRF_TIMER3->INTENCLR = TIMER_INTENSET_COMPARE4_Set << TIMER_INTENSET_COMPARE4_Pos;
  }
  //NRF_LOG_INFO("Unhandled TIMER3 Interrupt");
}

static void timeSyncInit(void)
{
  uint32_t       err_code;
  uint8_t        rf_address[5] = {0xDE, 0xAD, 0xBE, 0xEF, 0x19};
  ts_params_t    ts_params;

  ts_params.high_freq_timer[0] = NRF_TIMER3;
  ts_params.high_freq_timer[1] = NRF_TIMER2;
  ts_params.rtc             = NRF_RTC1;
  ts_params.egu             = NRF_EGU3;
  ts_params.egu_irq_type    = SWI3_EGU3_IRQn;
  ts_params.ppi_chg         = 0;
  ts_params.ppi_chns[0]     = 1;
  ts_params.ppi_chns[1]     = 2;
  ts_params.ppi_chns[2]     = 3;
  ts_params.ppi_chns[3]     = 4;
  ts_params.rf_chn          = 125; /* For testing purposes */
  memcpy(ts_params.rf_addr, rf_address, sizeof(rf_address));

  err_code = ts_init(&ts_params);
  APP_ERROR_CHECK(err_code);
  
  err_code = ts_enable();
  APP_ERROR_CHECK(err_code);
}

void timestamp_capture_init(void){
  nrf_ppi_channel_endpoint_setup(
    NRF_PPI_CHANNEL6,
    (uint32_t) nrf_egu_event_address_get(NRF_EGU0, NRF_EGU_EVENT_TRIGGERED0),
    (uint32_t) nrf_timer_task_address_get(NRF_TIMER2, NRF_TIMER_TASK_CAPTURE3));

  nrf_ppi_fork_endpoint_setup(
    NRF_PPI_CHANNEL6,
    (uint32_t) nrf_timer_task_address_get(NRF_TIMER3, NRF_TIMER_TASK_CAPTURE3)); 
  
  nrf_ppi_channel_enable(NRF_PPI_CHANNEL6);
}

void processQueue(void);

bool system_init(bool init_bt){
  bool ok = true;
  
  log_init(); // Causes very strong noise for some platforms??
  profile_init();
  timersInit();
  gpioInit();
  power_management_init();
  eventQueueInit();

  led_init();

  ok = ok && i2c_init();
  ok = ok && fg_init();
  
  #if SHIELD_ENABLED
  //mag_init();
  gyro_init();
  #endif
  
  ok = ok && accel_init();
  
  ok = ok && buzzer_init();
  ok = ok && motors_init();
  charger_init();

  ret_code_t err_code;
  err_code = app_timer_create(&resetTimer, APP_TIMER_MODE_SINGLE_SHOT, resetTimerCallback);
  APP_ERROR_CHECK(err_code);

  //buttons_leds_init(&erase_bonds);
  led_init();

  audioInit();

  if(init_bt){
    bleInit();
  
    timeSyncInit();
    timestamp_capture_init();
  }  
  // Initializes all time synchronized tasks
  ts_sync_tasks_init();

  // Initializes chirp offset detection for localization
  init_chirp_fft();

  nav_init();

  ok = ok && ir_init();
  APP_ERROR_CHECK_BOOL(ok);

  // Get fuel guage readings
  fg_update_current_measurements();
  
  // Wait for sensor calibration
#if SHIELD_ENABLED
  while(!gyro_ready()){
    idle_state_handle();
    processQueue();
  }
#endif
  
  while(!accel_ready()){
    idle_state_handle();
    processQueue();
  }

  return ok;
}

void print_sensor_info(){
  float battery_level = fg_get_current_battery_level();
  float soc = fg_get_current_soc();
  NRF_LOG_INFO("Current voltage: " NRF_LOG_FLOAT_MARKER "V\nCurrent state of charge: "
              NRF_LOG_FLOAT_MARKER"\n",
              NRF_LOG_FLOAT(battery_level),
              NRF_LOG_FLOAT(soc));
}

int task_time = 3;

#include "math.h"
#include "arm_math.h"
float interp_table[1000 + 5];

// Resample audio from S1 samples to S2 samples
void audio_resample(int16_t *buffer, uint16_t S1, uint16_t S2, int channels){
  if(S1 == S2) return;
  float step = 1.0 * S1 / S2;

  arm_q15_to_float(buffer, interp_table, S1);

  //NRF_LOG_RAW_INFO("Convert: %lld us\n", t2 - t1);

  arm_linear_interp_instance_f32 S = {S1, 0, 1, interp_table};
  float val = 0;
  
  // We only care about every m-th element
  for(int i = 0; i < S2; i++){
    buffer[i] = INT16_MAX * arm_linear_interp_f32(&S, val);
    val += step;
  }
}

/**@brief Function for application main entry.
 */
int main(void){
    // Initialize.
    bool init_bt = true;
    //bool init_bt = false;
    
    system_init(init_bt);
    print_sensor_info();

    bleAdvertisingStart();
    //nav_begin();

    //accel_enable_collision_detection(true);

    //motors_deinit();
    //accel_deinit();
  
    //#if SHIELD_ENABLED
    //  gyro_deinit();
    //#endif
  
    ////i2c_deinit();
    //i2s_deinit();
    ////audioDeInit();

    //led_deinit();
    //ir_disable();

    //accel_enable_collision_detection(true);
    //charger_start_station_entry();

    //nav_forward(5e6, 200, 1);
    //////delayMs(1005);
    //nav_rotate_angle(180);
    //////delayMs(500);
    //nav_rotate_angle_precise(90);
    //////delayMs(500);
    //nav_backward(1e6, 200, 1);
    ////delayMs(1005);
    //nav_rotate_time(2e6, 200);

    
    //ir_set_mode(IR_MODE_COUNTER);
    //ir_set_target_depth(100);
    //motors_forward(150);
    //ir_enable(false);

    //ir_set_mode(IR_MODE_EDGE_DETECTION);

    //uint8_t args[sizeof(uint64_t) + sizeof(int16_t)];
    //uint64_t time = 1e9;
    //((uint64_t *)args)[0] = time;
    //((int16_t *)args)[4] = 250;
    //nav_motion_update(MOTION_FORWARD, args, sizeof(uint64_t) + sizeof(uint16_t));

    //ir_enable(false);

    //nav_begin();

    for (;;){
        idle_state_handle();
        processQueue();
    }
}


void processQueue(void){
  if (!eventQueueEmpty()) {
    //NRF_LOG_RAW_INFO("%08d [main] Received event:%d\n", systemTimeGetUs(), eventQueueFront());
    switch(eventQueueFront()) {
      case EVENT_BLE_SEND_METADATA:
        ts_sync_task_send_metadata();
       break;

      case EVENT_AUDIO_MIC_DATA_READY:{
        //NRF_LOG_RAW_INFO("[audio] Audio data ready\n");
        uint8_t *buffer;
        uint8_t data_length;
        uint8_t fetched = 0;
        while(data_length = audioGetMicData(&buffer)){
          // Set audioStreamStarted to true
          fetched++;
          
          memcpy_fast(micData, buffer, PACKET_LENGTH);
          //if(tmp){
          //  for(int i = 0 ; i < 50 /*data_length/2*/; i++){
          //    NRF_LOG_RAW_INFO("%d ", (micData[2 * i + 1] << 8) + micData[2 * i]);
          //  }NRF_LOG_RAW_INFO("\n");
          //  tmp = false;
          //}
          // Sometimes a PDM buffer gets thrown into the ether?
          //uint32_t actualBufferCount = audioGetPdmBufferCount();
          //if (++expectedBufferCount != actualBufferCount) {
          //  //NRF_LOG_RAW_INFO("%08d [audio] expected(%d) != actual(%d)\n", systemTimeGetMs(), expectedBufferCount, actualBufferCount);
          //  for (int i = 0; i < (actualBufferCount - expectedBufferCount); i++) { blePushSequenceNumber(); }
          //  expectedBufferCount = actualBufferCount;
          //}          
          //NRF_LOG_RAW_INFO("%08d [ble] Length %d\n", systemTimeGetMs(), data_length);
          if(audio_get_mode() == AUDIO_MODE_STREAMING){
            assert(audioStreamStarted());
            if (bleBufferHasSpace(data_length)) {
              //NRF_LOG_RAW_INFO("%08d [ble] written %d samples to queue\n", systemTimeGetMs(), PACKET_LENGTH);
              bleSendData((uint8_t *) micData, data_length);
              //NRF_LOG_RAW_INFO("%08d [ble] buffer available bytes: %d\n", systemTimeGetMs(), bleGetRingBufferBytesAvailable());
              //NRF_LOG_RAW_INFO("%08d [ble] %d %d %d\n", 
              //          (micData[0] << 8) + micData[1],
              //          (micData[2] << 8) + micData[3],
              //          (micData[4] << 8) + micData[5]);
            } else {
              // No space, drop this data
              NRF_LOG_RAW_INFO("%08d [ble] dropped %d bytes\n", systemTimeGetMs(), data_length);
              blePushSequenceNumber();
            }
          }else if(audio_get_mode() == AUDIO_MODE_RECORDING){
            uint8_t *adjusted_ptr = micData;
            uint16_t adjusted_length;
            //NRF_LOG_RAW_INFO("%08d [main] Record\n", systemTimeGetMs());
            //NRF_LOG_RAW_INFO("%08d [main] m_audio_buffer_samples: %d\n", systemTimeGetMs(), m_audio_buffer_samples);
            // If recording is expected during this time
            if(save_recording(m_audio_buffer_samples, data_length, &adjusted_ptr, &adjusted_length)){              
              //NRF_LOG_RAW_INFO("%08d [main] Saving\n", systemTimeGetMs());
              //if(adjusted_length < 200)
              //  NRF_LOG_RAW_INFO("Storing %lld bytes (%lld samples)\n", adjusted_length, adjusted_length/2);
              // Save buffer
              if(s_recording.length == 0){
                s_recording.start_time = systemTimeGetUs();
              }
              recorder_add(&s_recording, adjusted_ptr, adjusted_length);
            }else if(audio_recording_finished(m_audio_buffer_samples)){
              //if(recorder_available(&s_recording)){
              //  //NRF_LOG_RAW_INFO("%08d Sending\n", systemTimeGetUs());
              //  recorder_send_all(&s_recording);
              //}else{
                
              //}
              //
              //NRF_LOG_RAW_INFO("%08d [main] Recorder length: %d\n", systemTimeGetMs(), s_recording.length);
              //ble_notify_recording_finished();
              eventQueuePush(EVENT_RECORDING_FINISHED);
            }
            m_audio_buffer_samples += data_length/2;
          }
        }
        break;
      }
    
      case EVENT_RECORDING_PROCESS_FINISHED:{
        bool flag = true;
        for(int i = 911; i < 915; i++){
          if(((int16_t*) s_recording.data)[i] != 0) flag = false;
        }
        if(flag) {
          NRF_LOG_RAW_INFO("%08d [main] ERROR\n", systemTimeGetUs(), s_recording.length);
          //APP_ERROR_CHECK_BOOL(0);
        }else{
          NRF_LOG_RAW_INFO("%08d [main] SAFE\n", systemTimeGetUs(), s_recording.length);
        }
        if(recorder_available(&s_recording) && m_audio_data_requested){
          NRF_LOG_RAW_INFO("%08d Sending %d samples\n", systemTimeGetUs(), s_recording.length);          
          APP_ERROR_CHECK_BOOL(audio_get_channels() * 3126 == s_recording.length);
          s_recording.requested = true;
          recorder_send_all(&s_recording);
        }
        }
        break;
      
      case EVENT_RECORDING_SEND_FINISHED:
        // Do nothing for now.
      break;

      case EVENT_RECORDING_FINISHED:
        if(ble_cus_indication_in_progress()){
          NRF_LOG_INFO("[ble_indicate_status]  ***** INDICATION IN PROGRESS *****");
        }
  
        if(nav_xcorr_stream_enabled()){
          // Begin chirp offset computation:
          
          if(audio_get_channels() == 2){
            // Get left channel
            recorder_deinterleave_channel(&s_recording, rec_single_channel_buffer, 0);
          
            uint64_t t1 = systemTimeGetUs();
            //uint16_t left_offset = detection_phase_left(rec_single_channel_buffer, s_recording.length/2);
            detection_phase_left(rec_single_channel_buffer, s_recording.length/2);
            uint64_t t2 = systemTimeGetUs();
            
            NRF_LOG_RAW_INFO("%08d [main] XCORR LEFT CHANNEL TIME: %lld\n", systemTimeGetMs(), t2 - t1);
            eventQueuePush(EVENT_CHIRP_DETECION_PHASE_RIGHT);
          }else{
            eventQueuePush(EVENT_CHIRP_DETECION_PHASE_FINAL);
          }
        }else{
          eventQueuePush(EVENT_RECORDING_PROCESS_FINISHED);
        }
      break;

      case EVENT_CHIRP_DETECION_PHASE_RIGHT:
        // Get right channel
        recorder_deinterleave_channel(&s_recording, rec_single_channel_buffer, 1);
      
        uint64_t t1 = systemTimeGetUs();
        //uint16_t left_offset = detection_phase_right(rec_single_channel_buffer, s_recording.length/2);
        detection_phase_right(rec_single_channel_buffer, s_recording.length/2);
        uint64_t t2 = systemTimeGetUs();
        NRF_LOG_RAW_INFO("%08d [main] XCORR RIGHT CHANNEL TIME: %lld\n", systemTimeGetMs(), t2 - t1);
        eventQueuePush(EVENT_CHIRP_DETECION_PHASE_FINAL);
      break;

      case EVENT_CHIRP_DETECION_PHASE_FINAL:
        if(nav_xcorr_stream_enabled()){
          uint16_t sample_offset;
          float32_t avg_offset;

          uint64_t t1 = systemTimeGetUs();
          //detection_phase2(&sample_offset, &avg_offset, ts_master());
          sample_offset = detection_phase_combine(ts_master(), 1);
          uint64_t t2 = systemTimeGetUs();

          NRF_LOG_RAW_INFO("%08d [main] COMBINE TIME: %lld\n", systemTimeGetMs(), t2 - t1);

          s_recording.end_time = systemTimeGetUs();

          nav_send_all(sample_offset, &s_recording);

          eventQueuePush(EVENT_RECORDING_PROCESS_FINISHED);
        }
      break;

      case EVENT_RECORDER_RESET:
        recorder_reset(&s_recording);
      break;

      case EVENT_AUDIO_START_CLICK:
        NRF_LOG_RAW_INFO("%08d [main] CHIRP\n", systemTimeGetMs())
        buzzer_play_chirp(1);
        // Chirp at 0 + 40 * 50ms = 2000ms
        //ts_sync_task_add(TS_TASK_SPK_START, MASTER_OVERFLOW_TRIGGER_COUNT + 40);
      break;

      case EVENT_AUDIO_MIC_NOTIFICATIONS_ENABLED:
        NRF_LOG_RAW_INFO("%08d [main] ENABLED AUDIO NOTIFICATIONS\n", systemTimeGetMs())
        m_audio_data_requested = true;
        resetBLE();
      break;

      case EVENT_AUDIO_MIC_NOTIFICATIONS_DISABLED:
        m_audio_data_requested = false;
        resetBLE();
        audioDeInit();
      break;

      case EVENT_SENSOR_NOTIFICATIONS_ENABLED:
        m_sensor_notifications_enabled = true;
      break;

      case EVENT_SENSOR_NOTIFICATIONS_DISABLED:
        m_sensor_notifications_enabled = false;
      break;

      case EVENT_BLE_DATA_STREAM_START:
        NRF_LOG_RAW_INFO("%08d [main] Streaming enabled\n", systemTimeGetMs());
        audio_set_mode(AUDIO_MODE_STREAMING);
        audio_ready();
        break;

      case EVENT_BLE_DATA_RECORD_START:
        m_audio_buffer_samples = 0;
        NRF_LOG_RAW_INFO("%08d [main] Recording enabled\n", systemTimeGetMs());
        audio_set_mode(AUDIO_MODE_RECORDING);
        reset_tracking();
        recorder_init(&s_recording, m_record_buffer, RECORDING_BUFFER_SIZE);
        audio_ready();
        break;

      case EVENT_BLE_DATA_STREAM_STOP:{
        // NVIC_SystemReset();
        // app_timer_start(resetTimer, APP_TIMER_TICKS(2000), NULL);
        audio_set_mode(AUDIO_MODE_NONE);
        resetBLE();
        break;
      }
      
      case EVENT_BLE_SEND_DATA_DONE:
        // BLE just finished, attempt to fill in more data
        //NRF_LOG_RAW_INFO("%08d [ble] [%d] (delayed) sent %d samples\n", systemTimeGetMs(), getSequenceNumber(), PDM_DECIMATION_BUFFER_LENGTH);
        //send();
        //NRF_LOG_RAW_INFO("%08d [ble] buffer available bytes: %d\n", systemTimeGetMs(), bleGetRingBufferBytesAvailable());
        //if(audio_get_mode() == AUDIO_MODE_STREAMING){
        //  send();
        //}else if(audio_get_mode() == AUDIO_MODE_RECORDING){
        //  if(s_recording.requested && recorder_available(&s_recording)){
        //    recorder_send_all(&s_recording);
        //  }
        //  //if(nav_xcorr_stream_enabled() && ble_xcorr_available()){
        //  //  ble_send_status_update_data();
        //  //}
        //}

        if(audio_get_mode() == AUDIO_MODE_STREAMING && ble_audio_stream_buffer_available()){
          send();
        }else if(audio_get_mode() == AUDIO_MODE_RECORDING &&
                 s_recording.requested &&
                 recorder_available(&s_recording)){
          recorder_send_all(&s_recording);
        }else if(ble_status_notification_buffer_available()){
          ble_notification_buffer_process();
        }else if(ble_status_indication_buffer_available()){
          ble_indication_buffer_process();
        }

        break;

      case EVENT_BLE_IDLE:
        powerEnterSleepMode();
        break;

      case EVENT_BLE_DISCONNECTED:
        NRF_LOG_RAW_INFO("Disconnected\n");
        //NRF_TIMER3->EVENTS_COMPARE[4] = 0; // What is this doing??
        NVIC_SystemReset();
        break;

      case EVENT_TIMESYNC_MASTER_ENABLE:
        ts_tasks_set_role(TS_ROLE_MASTER);
        break;

      case EVENT_TIMESYNC_SLAVE_ENABLE:
        ts_tasks_set_role(TS_ROLE_SLAVE);
      break;
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

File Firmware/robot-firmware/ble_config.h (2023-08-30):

#ifndef _BLE_CFG_H_
#define _BLE_CFG_H_

#include "audio_config.h"
#include "sdk_config.h"

// BLE
#define DEVICE_NAME                     "shio"                                  /**< Name of device. Will be included in the advertising data. */
#define MANUFACTURER_NAME               "uw"                                    /**< Manufacturer. Will be passed to Device Information Service. */
#define APP_ADV_INTERVAL                300                                     /**< The advertising interval (in units of 0.625 ms. This value corresponds to 187.5 ms). */

#define APP_ADV_DURATION                18000                                   /**< The advertising duration (180 seconds) in units of 10 milliseconds. */
#define APP_BLE_OBSERVER_PRIO           3                                       /**< Application's BLE observer priority. You shouldn't need to modify this value. */
#define APP_BLE_CONN_CFG_TAG            1                                       /**< A tag identifying the SoftDevice BLE configuration. */

#define MIN_CONN_INTERVAL               MSEC_TO_UNITS(7.5, UNIT_1_25_MS)        /**< Minimum acceptable connection interval (0.1 seconds). */
#define MAX_CONN_INTERVAL               MSEC_TO_UNITS(7.5, UNIT_1_25_MS)        /**< Maximum acceptable connection interval (0.2 second). */
#define SLAVE_LATENCY                   0                                       /**< Slave latency. */
#define CONN_SUP_TIMEOUT                MSEC_TO_UNITS(720, UNIT_10_MS)         /**< Connection supervisory timeout (1 seconds). */
#define IOS_MAX_ATT_MTU_SIZE_BYTES      (182)

#define FIRST_CONN_PARAMS_UPDATE_DELAY  APP_TIMER_TICKS(1000)                   /**< Time from initiating event (connect or start of notification) to first time sd_ble_gap_conn_param_update is called (5 seconds). */
#define NEXT_CONN_PARAMS_UPDATE_DELAY   APP_TIMER_TICKS(40000)                  /**< Time between each call to sd_ble_gap_conn_param_update after the first call (30 seconds). */
#define MAX_CONN_PARAMS_UPDATE_COUNT    3                                       /**< Number of attempts before giving up the connection parameter negotiation. */

#define SEC_PARAM_BOND                  1                                       /**< Perform bonding. */
#define SEC_PARAM_MITM                  0                                       /**< Man In The Middle protection not required. */
#define SEC_PARAM_LESC                  0                                       /**< LE Secure Connections not enabled. */
#define SEC_PARAM_KEYPRESS              0                                       /**< Keypress notifications not enabled. */
#define SEC_PARAM_IO_CAPABILITIES       BLE_GAP_IO_CAPS_NONE                    /**< No I/O capabilities. */
#define SEC_PARAM_OOB                   0                                       /**< Out Of Band data not available. */
#define SEC_PARAM_MIN_KEY_SIZE          7                                       /**< Minimum encryption key size. */
#define SEC_PARAM_MAX_KEY_SIZE          16                                      /**< Maximum encryption key size. */

#define PACKET_LENGTH                   (NRF_SDH_BLE_GATT_MAX_MTU_SIZE - 5)

// Buttons and LED
#define USER_BUTTON 0                                                           // 0 is the first button in nordic code

// Stack
#define DEAD_BEEF                       0xDEADBEEF                              /**< Value used as error code on stack dump, can be used to identify stack location on stack unwind. */




#endif

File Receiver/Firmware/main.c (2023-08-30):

/**
 * Copyright (c) 2016 - 2021, Nordic Semiconductor ASA
 *
 * All rights reserved.
 *
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
 * 3. Neither the name of Nordic Semiconductor ASA nor the names of its
 *    contributors may be used to endorse or promote products derived from this
 *    software without specific prior written permission.
 *
 * 4. This software, with or without modification, must only be used with a
 *    Nordic Semiconductor ASA integrated circuit.
 *
 * 5. Any software provided in binary form under this license must not be reverse
 *    engineered, decompiled, modified and/or disassembled.
 *
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
 */
#include <stdio.h>
#include <stdint.h>
#include <stdbool.h>
#include "nordic_common.h"
#include "app_error.h"
#include "app_uart.h"
#include "app_timer.h"
#include "app_util.h"
#include "nrf_drv_clock.h"
#include "nrf_pwr_mgmt.h"
#include "app_usbd.h"

#include "nrf_log.h"
#include "nrf_log_ctrl.h"
#include "nrf_log_default_backends.h"

#include "event.h"
#include "timers.h"
#include "ble_cus.h"
#include "usb.h"
#include "peripheral.h"
#include "bsp_btn_ble.h"

static uint8_t usb_args_buffer[256];
static bool m_ble_tx_sent_requested = false;

#define RUN_TESTS 0

/**@brief Function for handling asserts in the SoftDevice.
 *
 * @details This function is called in case of an assert in the SoftDevice.
 *
 * @warning This handler is only an example and is not meant for the final product. You need to analyze
 *          how your product is supposed to react in case of assert.
 * @warning On assert from the SoftDevice, the system can only recover on reset.
 *
 * @param[in] line_num     Line number of the failing assert call.
 * @param[in] p_file_name  File name of the failing assert call.
 */
void assert_nrf_callback(uint16_t line_num, const uint8_t * p_file_name)
{
    app_error_handler(0xDEADBEEF, line_num, p_file_name);
}

/**
 * @brief Function for handling shutdown events.
 *
 * @param[in]   event       Shutdown type.
 */
static bool shutdown_handler(nrf_pwr_mgmt_evt_t event)
{
    ret_code_t err_code;

    err_code = bsp_indication_set(BSP_INDICATE_IDLE);
    APP_ERROR_CHECK(err_code);

    switch (event)
    {
        case NRF_PWR_MGMT_EVT_PREPARE_WAKEUP:
            // Prepare wakeup buttons.
            err_code = bsp_btn_ble_sleep_mode_prepare();
            APP_ERROR_CHECK(err_code);
            break;

        default:
            break;
    }

    return true;
}

NRF_PWR_MGMT_HANDLER_REGISTER(shutdown_handler, APP_SHUTDOWN_HANDLER_PRIORITY);

/**@brief Function for handling events from the BSP module.
 *
 * @param[in] event  Event generated by button press.
 */
void bsp_event_handler(bsp_event_t event)
{
    ret_code_t err_code;

    switch (event)
    {
        case BSP_EVENT_SLEEP:
            nrf_pwr_mgmt_shutdown(NRF_PWR_MGMT_SHUTDOWN_GOTO_SYSOFF);
            break;

        case BSP_EVENT_DISCONNECT:
            //err_code = sd_ble_gap_disconnect(m_ble_nus_c.conn_handle,
            //                                 BLE_HCI_REMOTE_USER_TERMINATED_CONNECTION);
            if (err_code != NRF_ERROR_INVALID_STATE)
            {
                APP_ERROR_CHECK(err_code);
            }
            break;

        default:
            break;
    }
}

/**@brief Function for initializing buttons and leds. */
static void buttons_leds_init(void)
{
    ret_code_t err_code;
    bsp_event_t startup_event;

    err_code = bsp_init(BSP_INIT_LEDS, bsp_event_handler);
    APP_ERROR_CHECK(err_code);

    err_code = bsp_btn_ble_init(NULL, &startup_event);
    APP_ERROR_CHECK(err_code);
}


/**@brief Function for initializing the nrf log module. */
static void log_init(void)
{
    ret_code_t err_code = NRF_LOG_INIT(NULL);
    APP_ERROR_CHECK(err_code);

    NRF_LOG_DEFAULT_BACKENDS_INIT();
}


/**@brief Function for initializing power management.
 */
static void power_management_init(void)
{
    ret_code_t err_code;
    err_code = nrf_pwr_mgmt_init();
    APP_ERROR_CHECK(err_code);
}

/**@brief Function for handling the idle state (main loop).
 *
 * @details Handles any pending log operations, then sleeps until the next event occurs.
 */
static void idle_state_handle(void)
{
    if (NRF_LOG_PROCESS() == false)
    {
        nrf_pwr_mgmt_run();
    }
}

void processQueue();

#if RUN_TESTS

#include "ringbuffer.h"
#define RB_SIZE (4096*2)
uint8_t _rb_stack[RB_SIZE];

#define TEST_ARR_LENGTH 5000
uint8_t input[TEST_ARR_LENGTH ];
uint8_t output[TEST_ARR_LENGTH ];

bool test_rb_check(ringbuffer_t *r, uint8_t* arr){
  for(int i = 0; i < TEST_ARR_LENGTH; i++){
    if(rb_at(r, i) != arr[i]){
      return false;
    }
  }
  return true;
}


bool test_arrays_equal(uint8_t *b, uint8_t* arr, int n){
  for(int i = 0; i < n; i++){
    if(b[i] != arr[i]){
      return false;
    }
  }
  return true;
}

void test_rb_heap_stack(void){
  ringbuffer_t rb_heap, rb_stack;

  rb_create(&rb_heap, RB_SIZE);
  rb_init(&rb_stack, _rb_stack, RB_SIZE);

  uint64_t t1, t2, t3;
  
  for(int i = 0; i < TEST_ARR_LENGTH; i++){
    input[i] = rand() % 256;
  }

  t1 = systemTimeGetUs();
  
  rb_put(&rb_heap, input, TEST_ARR_LENGTH);
  
  t2 = systemTimeGetUs();

  rb_put(&rb_stack, input, TEST_ARR_LENGTH);

  t3 = systemTimeGetUs();

  NRF_LOG_RAW_INFO("[main] RB HEAP TEST ")
  if(test_rb_check(&rb_heap, input)){
    NRF_LOG_RAW_INFO("SUCCEEDED ")
  }else{
   NRF_LOG_RAW_INFO("FAILED ")
  }
  NRF_LOG_RAW_INFO("Time taken: %d\n", t2 - t1)
  
  NRF_LOG_RAW_INFO("[main] RB STACK TEST ")
  
  if(test_rb_check(&rb_stack, input)){
    NRF_LOG_RAW_INFO("SUCCEEDED ")
  }else{
    NRF_LOG_RAW_INFO("FAILED ")
  }
  NRF_LOG_RAW_INFO("Time taken: %d\n", t3 - t2)  
}
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

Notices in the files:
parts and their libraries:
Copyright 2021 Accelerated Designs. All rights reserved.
